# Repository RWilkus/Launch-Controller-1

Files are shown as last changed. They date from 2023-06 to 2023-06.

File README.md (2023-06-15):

# Launch-Controller-1
Model Rocket Launch Controller

Designer: Ryan Wilkus

Audience: Cub Scouts/Scouts BSA

LaunchControllerRevA

(Rev A Image)

Ordering:

PCB - [PCBWay.com](https://www.pcbway.com/QuickOrderOnline.aspx)
 - Upload Gerbers
 - 2 layer, 1.6mm thickness, FR-4 material, 1oz Cu, Black soldermask, White silkscreen, HASL with Lead surface finish
 - Adjust board quantity to find maximum boards per price. 10 boards was the same price as 1.



Parts - [Digikey.com](https://www.digikey.com/ordering/shoppingcart?lang=en)
 - Upload LaunchController1 BOM.xlsx to purchase

3D printing:

Resolution: 0.2mm, Infill: 20%, Filiment: 1.75mm Supports: Yes, Rafts: Yes, 

PCB Assembly Instructions:

Assemble and solder in order

R1-R6: Bidirectional so orientation doesn't matter. 

     (R1,R4,R5) 300 Ohm: Orange, Black, Brown, Gold
     
     (R2,R3,R6) 4.7k Ohm: Yellow, Purple, Red, Gold
     
D1/D2: Bidirectional so orientation doesn't matter

PTC1: Bidirectional so orientation doesn't matter

LED1/LED2: LED1= Red, LED2=Green. Long lead goes into the positive symbol(+)

Q1/Q2: Bend outside leads to match hole spacing. Verify larger flat side matches flat silkscreen. 

J1: Orient connector to edge of board

SW1: Orientation doesn't matter. 

SW2: Make sure SW2 flat side matches silkscreen

BT1: Use double sided tape or super glue to secure to board. Solder leads from the top side.

Cutoff excess component leads

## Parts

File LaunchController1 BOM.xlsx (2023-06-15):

Index | Manufacturer Part Number | Manufacturer Name | Description | Attrition % | Requested Quantity 1 | Pack Quantity 1 | Pack Type 1 | Digi-Key Part Number 1 | Unit Price 1 | Extended Price 1 | Minimum Order Quantity 1 | Customer Reference | Reference Designator | Part Status | RoHS Status | Original Part numbers
1 | 691137710002 | Würth Elektronik | TERM BLK 2POS SIDE ENTRY 5MM PCB |  | 1 | 1 | Box | 732-10955-ND | 0.41000 | $0.41 | 1 | J1 |  | Active | ROHS3 Compliant | 732-10955-ND
2 | D6R40 F2 LFS | C&K | SWITCH PUSH SPST-NO 0.1A 32V |  | 1 | 1 | Tray | 401-1992-ND | 1.08000 | $1.08 | 1 | SW2 |  | Active | ROHS3 Compliant | 401-1992-ND
3 | BU-34 | Mueller Electric Co | GATOR CLIP STEEL NON-INSUL 5A |  | 2 | 2 | Bulk | 314-1017-ND | 0.54000 | $1.08 | 1 |  |  | Active | RoHS Compliant | 314-1017-ND
4 | C566D-RFE-CV0X0BB1 | CreeLED, Inc. | LED RED DIFFUSED 5MM OVAL T/H |  | 1 | 1 | Bulk | C566D-RFE-CV0X0BB1-ND | 0.18000 | $0.18 | 1 | LED1 |  | Active | RoHS Compliant | C566D-RFE-CV0X0BB1-ND
5 | C5SMF-GJE-CX14Q7T2 | CreeLED, Inc. | LED GREEN CLEAR 5MM OVAL T/H |  | 1 | 1 | Cut Tape (CT) | C5SMF-GJE-CX14Q7T2CT-ND | 0.30000 | $0.30 | 1 | LED2 |  | Active | RoHS Compliant | C5SMF-GJE-CX14Q7T2CT-ND
6 | 2477 | Keystone Electronics | BATTERY HOLDER AA 4 CELL PC PIN |  | 1 | 1 | Bulk | 36-2477-ND | 1.87000 | $1.87 | 1 | BT1 |  | Active | ROHS3 Compliant | 36-2477-ND
7 | ZTX718 | Diodes Incorporated | TRANS PNP 20V 2.5A E-LINE |  | 2 | 2 | Bulk | ZTX718-ND | 0.77000 | $1.54 | 1 | Q1, Q2 |  | Active | ROHS3 Compliant | ZTX718-ND
8 | ANT11SF1CQE | CIT Relay and Switch | SWITCH TOGGLE SPDT 5A 120V |  | 1 | 1 | Bulk | 2449-ANT11SF1CQE-ND | 1.26000 | $1.26 | 1 | SW1 |  | Active | RoHS Compliant | 2449-ANT11SF1CQE-ND
9 | P6KE7.5CA/B | YAGEO | P6KE, DO-204AC, 6.4V, 11.3V, BOX |  | 2 | 2 | Box | 13-P6KE7.5CA/B-ND | 0.38000 | $0.76 | 1 | D1, D2 |  | Active | ROHS3 Compliant | 13-P6KE7.5CA/B-ND
10 | 0ZRG0120FF2E | Bel Fuse Inc. | PTC RESET FUSE 30V 1.2A RADIAL |  | 1 | 1 | Cut Tape (CT) | 507-0ZRG0120FF2ECT-ND | 0.44000 | $0.44 | 1 | PTC1 |  | Active | ROHS3 Compliant | 507-0ZRG0120FF2ECT-ND
11 | CF14JT300R | Stackpole Electronics Inc | RES 300 OHM 5% 1/4W AXIAL |  | 3 | 3 | Cut Tape (CT) | CF14JT300RCT-ND | 0.10000 | $0.30 | 1 | R1, R4, R5 |  | Active | ROHS3 Compliant | CF14JT300RCT-ND
12 | CF14JT4K70 | Stackpole Electronics Inc | RES 4.7K OHM 5% 1/4W AXIAL |  | 3 | 3 | Cut Tape (CT) | CF14JT4K70CT-ND | 0.10000 | $0.30 | 1 | R2, R3, R6 |  | Active | ROHS3 Compliant | CF14JT4K70CT-ND

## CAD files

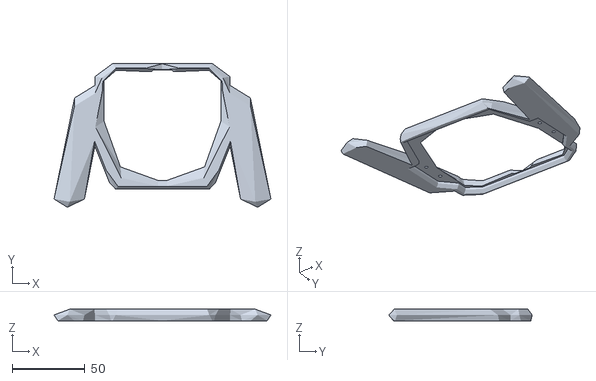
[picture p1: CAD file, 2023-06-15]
Enclosure/Launch Controller 1 Rev A.stl
149.6 x 98.9 x 8.00

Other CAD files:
Enclosure/Launch Controller 1.skp

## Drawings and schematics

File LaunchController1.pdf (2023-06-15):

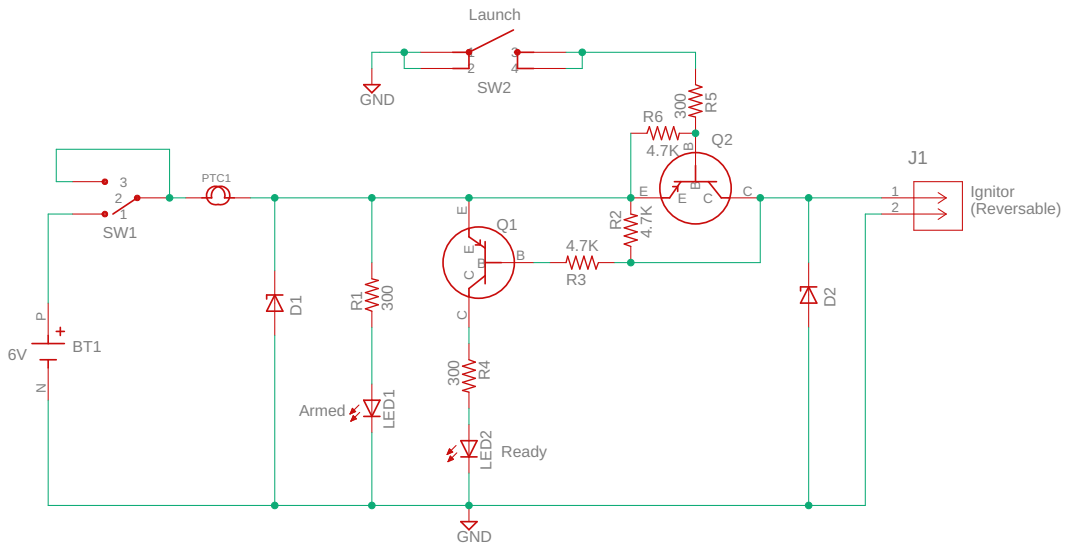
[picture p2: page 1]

Document Number: 2050N-23-1 | REV: B

Date: 6/15/23 12:23 PM | Sheet: 1/1

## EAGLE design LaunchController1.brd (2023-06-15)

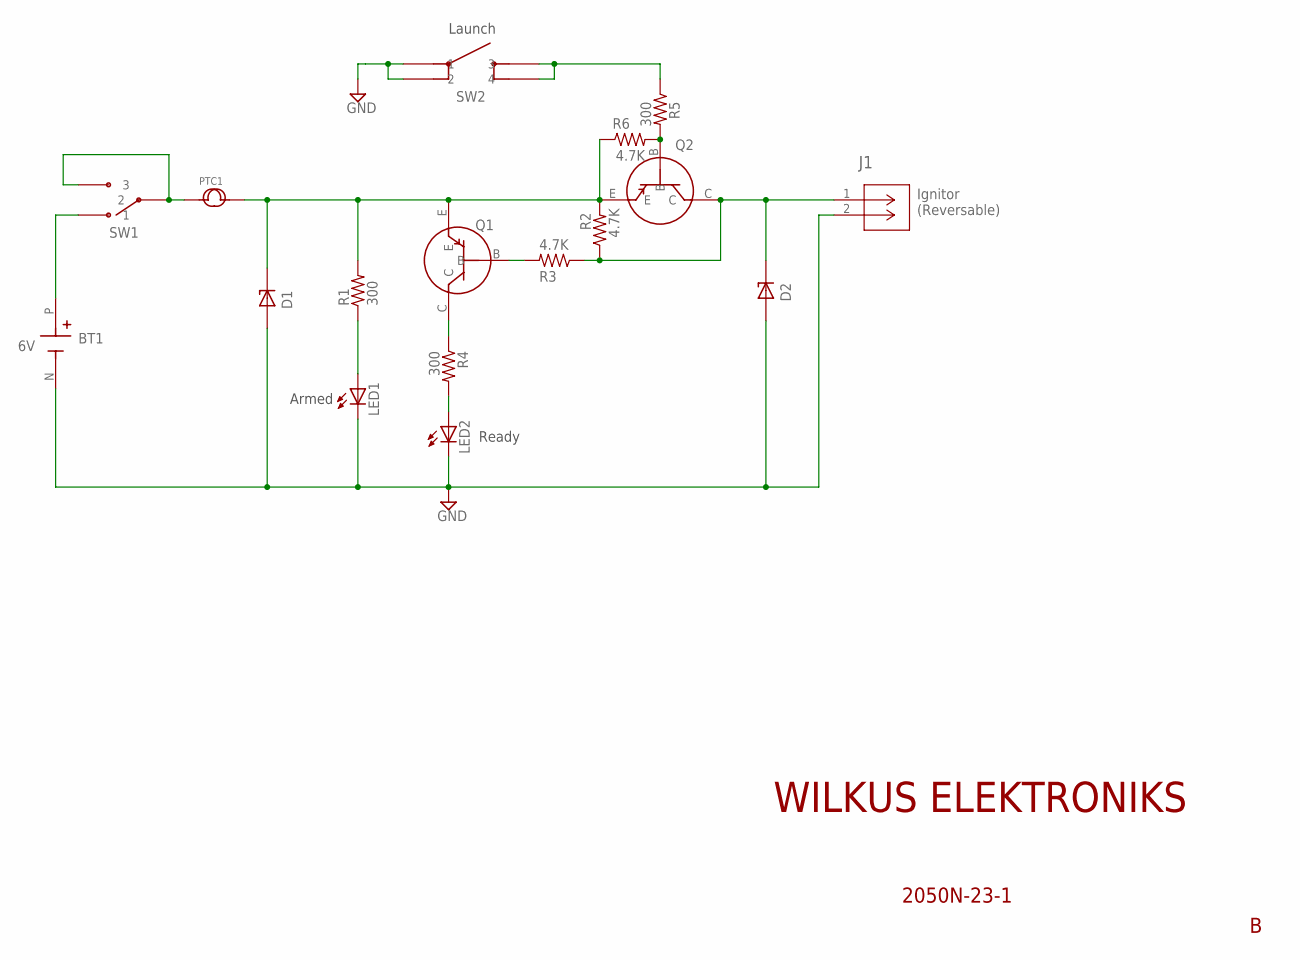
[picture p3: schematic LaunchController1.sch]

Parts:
BT1: 6V; BAT_2477
D1, D2: P6KE75CA; DIOAD1300W80L670D310
J1: 691137710002; CONN2_710002_WRE
LED1, LED2: LED5MM
PTC1: 0ZRG0120FF2E; 0ZRG
Q1, Q2: BJT_PNP; TO92-
R1, R4, R5: 300; 0309/12
R2, R3, R6: 4.7K; 0309/12
SW1: ANT11SF1CQE
SW2: D6R40F2LFS

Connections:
GND: BT1.N (NEG), D1.A, D2.A, J1.2, LED1.K (C), LED2.K (C), SW2.P$1 (1), SW2.P$2 (2)
IGNTR_HOT: D2.C, J1.1, Q2.C, R2.1, R3.1
unnamed: Q1.B, R3.2
unnamed: PTC1.1, SW1.P$2 (2), SW1.P$3 (3)
unnamed: Q2.B, R5.2, R6.2
unnamed: LED1.A, R1.1
unnamed: R5.1, SW2.P$3 (3), SW2.P$4 (4)
unnamed: D1.C, PTC1.2, Q1.E, Q2.E, R1.2, R2.2, R6.1
unnamed: LED2.A, R4.2
unnamed: Q1.C, R4.1
PWR: BT1.P (POS), SW1.P$1 (1)

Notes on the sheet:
Ready
Armed
Launch
Ignitor (Reversable)

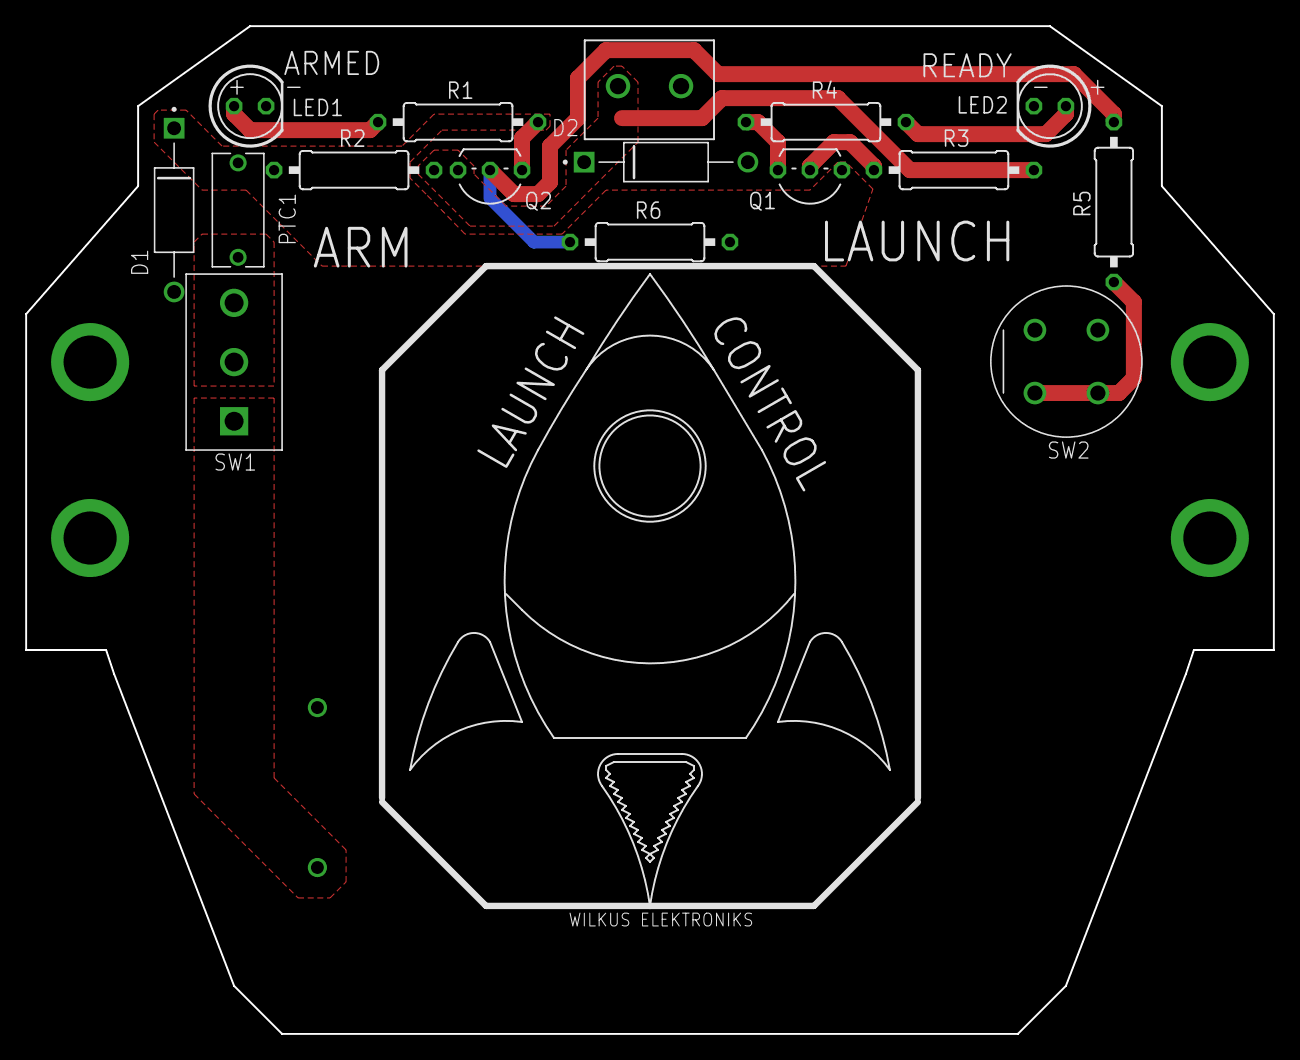
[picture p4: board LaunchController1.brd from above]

Board: 2 copper layers, 99.1 x 80.0 mm, 17 parts (1 on the bottom side), 11 nets.

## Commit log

2023-06-15 Add files via upload
    Rev B commit - Working prototype
    [LaunchController1.brd, LaunchController1.sch]
2023-06-15 Add files via upload
    Rev B BOM commit
    [LaunchController1 BOM.xlsx]
2023-06-15 Add files via upload
    3D print files
    [Launch Controller 1 Rev A.stl, Launch Controller 1.skp]

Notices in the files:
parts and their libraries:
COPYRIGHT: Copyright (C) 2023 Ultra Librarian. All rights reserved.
